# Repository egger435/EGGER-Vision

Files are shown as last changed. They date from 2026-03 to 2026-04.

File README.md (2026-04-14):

# EGGER Vision

基于Unity上位机 + STM32下位机 + 树莓派视觉模块的远程遥控车项目

## 一、ta是神马东西？

<p align="center">
    <a>
        
        <br>
    </a>
</p>

视频地址：https://www.bilibili.com/video/BV1trXPBxEZR

&emsp;&emsp;这是一个**完整远程控制小车项目**，包含：

* stm32控制板硬件连接电路
* 车身3d打印结构
* 嵌入式控制程序
* Unity可视化客户端

&emsp;&emsp;实现了：

* 手柄/键盘双模式远程控制
* 实时视频流传输

## 二、ta的组成是？

### 2.1 用了哪些东西

&emsp;&emsp;***硬件部分***：

  1. **stm32f103c8t6最小系统板**: 控制电机、舵机、处理底层控制逻辑
  2. **tb6612电机驱动模块**: 驱动电机
  3. **树莓派4b视觉模块（包括摄像头）**: 采集并发送视频流、接收控制信号
  4. **SG90舵机**: 转向前桥控制、摄像头转向
  5. **lm2596电源模块**: 供电
  6. **12V 18650可充电池组**：供电
  7. **拼夕夕的带有转向前桥的底盘**
  8. **3D打印结构**: 支架、连接件、挂车等

&emsp;&emsp;***软件部分***:

  1. **Unity2022.3.62f2c1**: 远程控制客户端开发
  2. **基于UDP的Unity和树莓派远程通信**: 这部分可以查看我的另一个仓库
     https://github.com/egger435/Unity-Pi-connect
  3. **在EIDE中使用库函数开发的stm32**

### 2.2 小车的架构

<p align="center">
    <a>
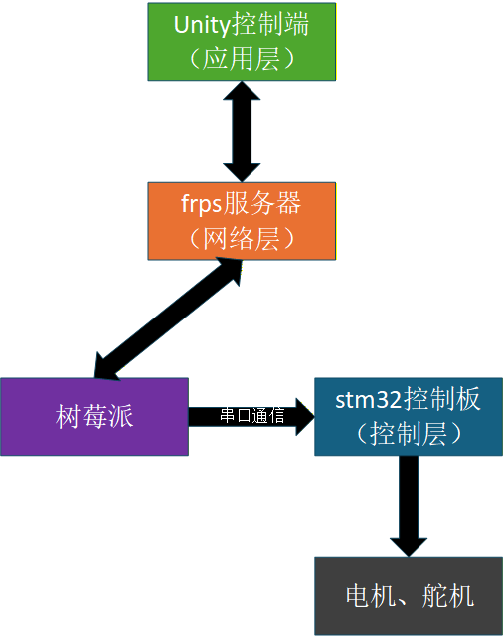
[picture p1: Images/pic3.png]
        
        <br>
    </a>
</p>

### 2.3 项目的架构

#### * Board文件夹

&emsp;&emsp;stm32控制板PCB设计文件, 线路就是简单的连连看。初中生来了都能看懂。

#### * Pi文件夹

&emsp;&emsp;树莓派视频流捕获和传输以及接收控制信号的代码

#### * SolidWorksFiles文件夹

&emsp;&emsp;***除了底盘外***的整车的3D结构模型, 包括3D打印件

#### * STM32文件夹

&emsp;&emsp;在EIDE中使用库函数开发的嵌入式控制代码

#### * UnityClient文件夹

&emsp;&emsp;Unity控制客户端工程文件

## 三、ta是怎么工作的

<p align="center">
    <a>
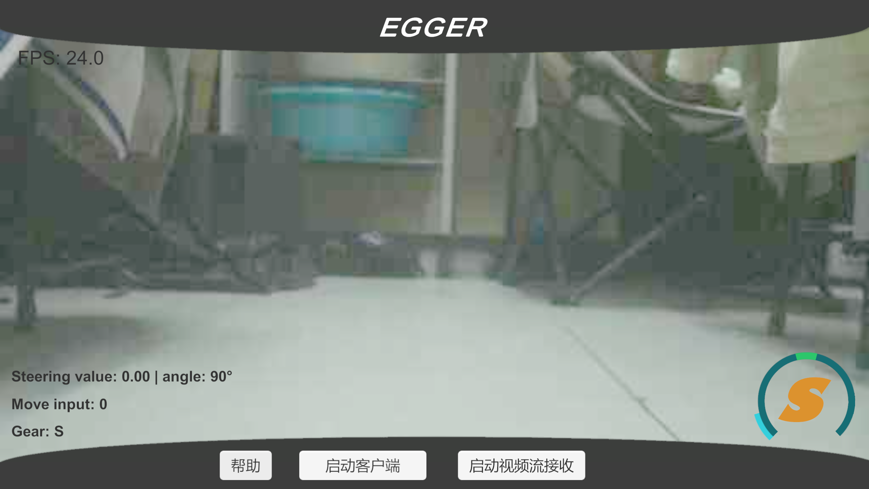
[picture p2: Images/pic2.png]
        
        <br>
    </a>
</p>

&emsp;&emsp;首先，Unity客户端会读取同目录下的`client_config`配置文件，得到服务器IP地址等信息。

&emsp;&emsp;然后，启动客户端的时候就会根据配置文件上的信息初始化。接着等待树莓派程序启动就可以接收视频流了。

&emsp;&emsp;简单来说就是，用户可以在Unity客户端实时看到画面，然后用手柄就能控制小车了。无论用户在哪，只要有网络就行。

&emsp;&emsp;信号流的传递：手柄 → Unity → FRPS服务器 → 树莓派 → stm32控制板

## ta的广告语

* 拖了个挂车，有**更大的储物空间**🚚
* 舵机控制转向加线性电门扳机，带来**更精准的操控**🦽
* 前置摄像头，拥有第一人称的**驾驶乐趣**🏎️
* 远程网络通信，能让你**在地球另一端控制它**🌍
* 还有后视镜，**足不出户**练习停车技巧
* 堪比奥迪夸戳的全史四驱系统:P

## 用户评价

某个不透露姓名的买家：

已购入，不建议入手[发怒]

速度太慢了，本来买来还想帮我跑校园跑的，结果比我走的还慢，别叫Vision叫蜗牛吧[发怒]

有转向前桥却没有阿克曼转向，也没有差速器，过弯表现一塌糊涂，转弯半径比我奶奶的破三轮都大[发怒]

延迟太不稳定了，一到信号不好的地方帧率就蹭蹭掉[发怒]

画质太差了，纯纯马赛克

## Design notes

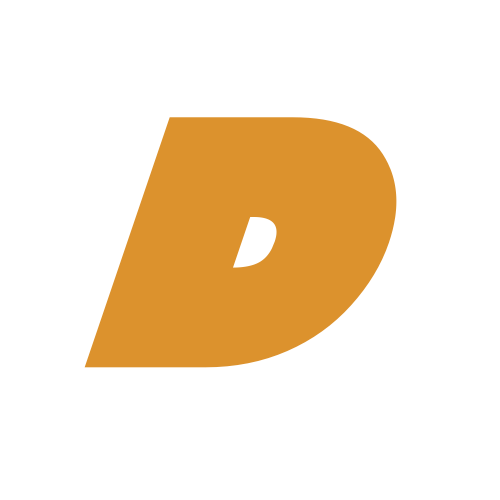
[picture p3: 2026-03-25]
UnityClient/Assets/Resource/D.png

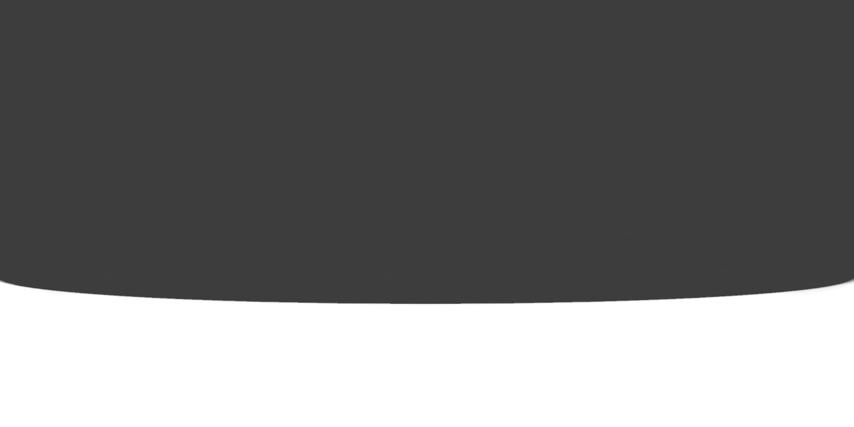
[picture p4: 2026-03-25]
UnityClient/Assets/Resource/upImage.png

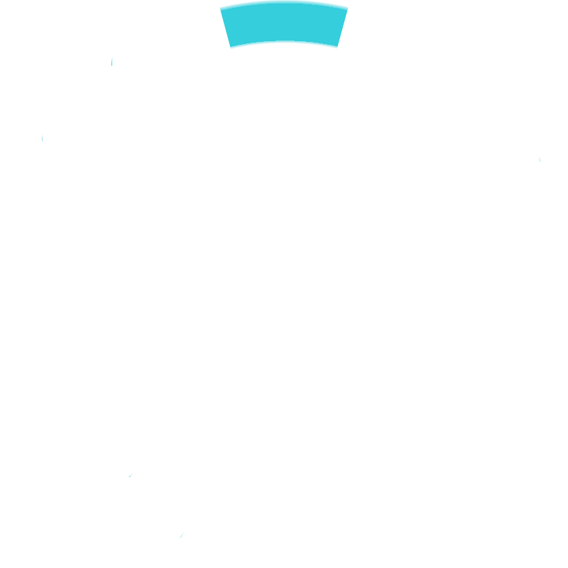
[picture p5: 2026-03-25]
UnityClient/Assets/Resource/steeringPos.png

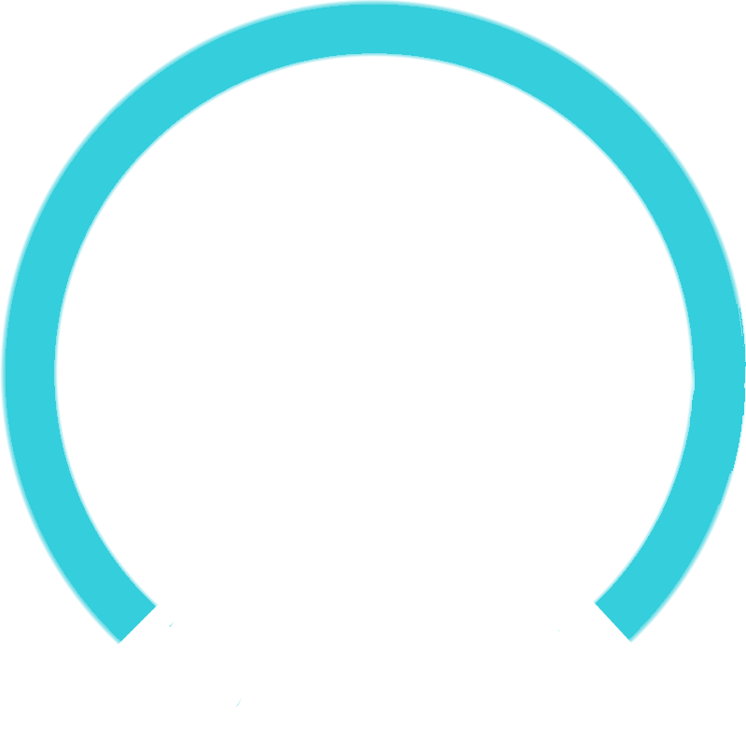
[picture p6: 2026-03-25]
UnityClient/Assets/Resource/Fill.png

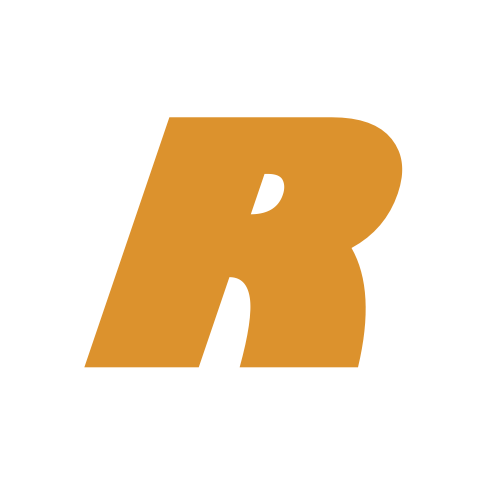
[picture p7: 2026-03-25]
UnityClient/Assets/Resource/R.png

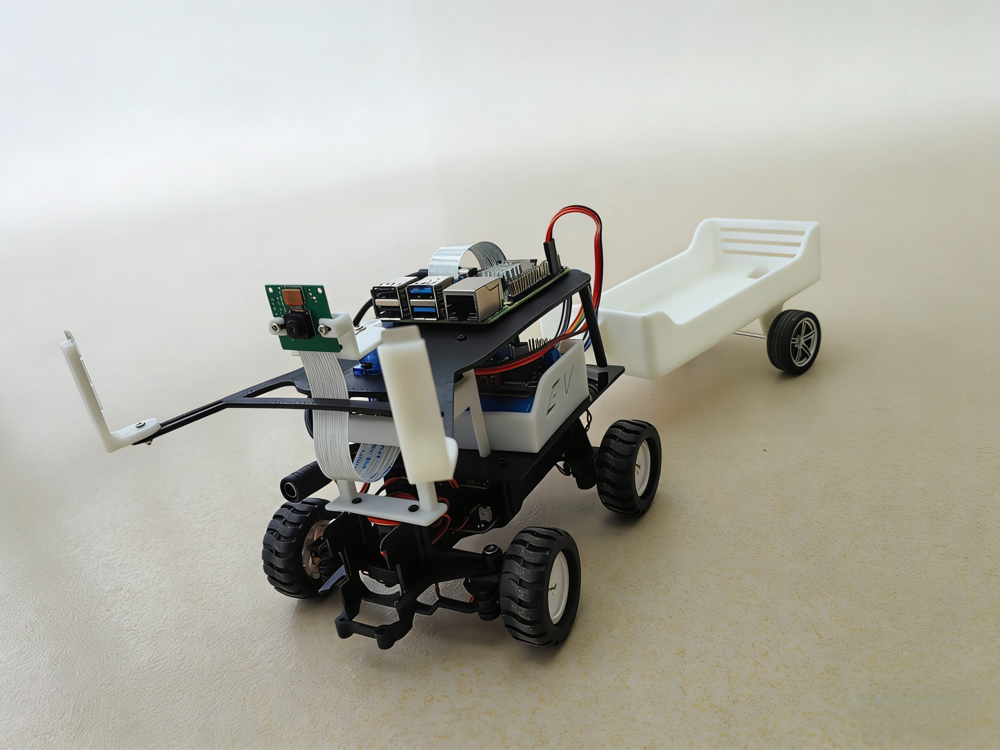
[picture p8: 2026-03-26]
UnityClient/Assets/Resource/bkg.png

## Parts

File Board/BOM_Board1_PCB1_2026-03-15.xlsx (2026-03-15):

No. | Quantity | Comment | Designator | Footprint | Value | Manufacturer Part | Manufacturer | Supplier Part | Supplier
1 | 3 | 2.54-1*3P针 | H1,H2,H3 | HDR-TH_3P-P2.54-V-M-1 |  | 2.54-1*3P针 | BOOMELE(博穆精密) | C49257 | LCSC
2 | 1 | PZ2.54-2*5 | H4 | HDR-TH_10P-P2.54-V-M-R2-C5-S2.54-1 |  | PZ2.54-2*5 | ZHOURI(洲日) | C5156677 | LCSC
3 | 1 | 1kΩ | R1 | R0603 | 1kΩ | 0603WAF1001T5E | UNI-ROYAL(厚声) | C21190 | LCSC
4 | 4 | KH-2.54FH-1X20P-H8.5 | U1,U2,U8,U9 | HDR-TH_20P-P2.54-V-F-2 |  | KH-2.54FH-1X20P-H8.5 | kinghelm(金航标) | C2905423 | LCSC
5 | 1 | PZ2.54-2*4 | U7 | HDR-TH_8P-P2.54-V-M-R2-C4-S2.54 |  | PZ2.54-2*4 | ZHOURI(洲日) | C5156676 | LCSC
6 | 4 | ZX-MX1.25-2PZZ | U10,U11,U12,U13 | CONN-TH_2P-P1.25_MEGASTAR_ZX-MX1.25-2PZZ |  | ZX-MX1.25-2PZZ | Megastar(兆星) | C7430458 | LCSC
7 | 1 | KT-0603R | 状态LED | LED_0603 |  | KT-0603R | KENTO | C2286 | LCSC

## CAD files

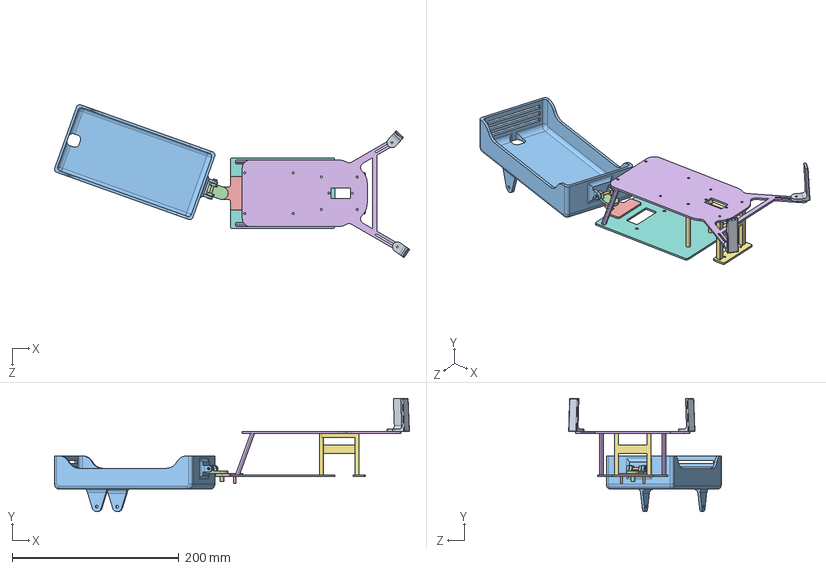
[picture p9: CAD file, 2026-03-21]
SolidWorksFiles/装配.SLDASM
425.7 x 135.9 x 183.2 mm
底板(非舵机转向板)
二层支架_2
二层板
挂车连接件
挂车连接件2
挂车
挂车连接件3
后视镜 x 2

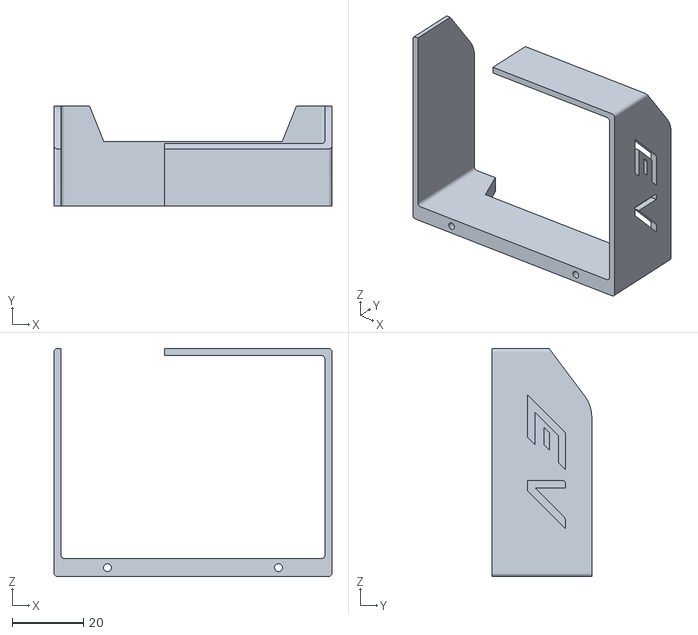
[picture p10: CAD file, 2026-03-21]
SolidWorksFiles/3dprint/电源固定件_3dprint.STL
78.0 x 28.0 x 64.0

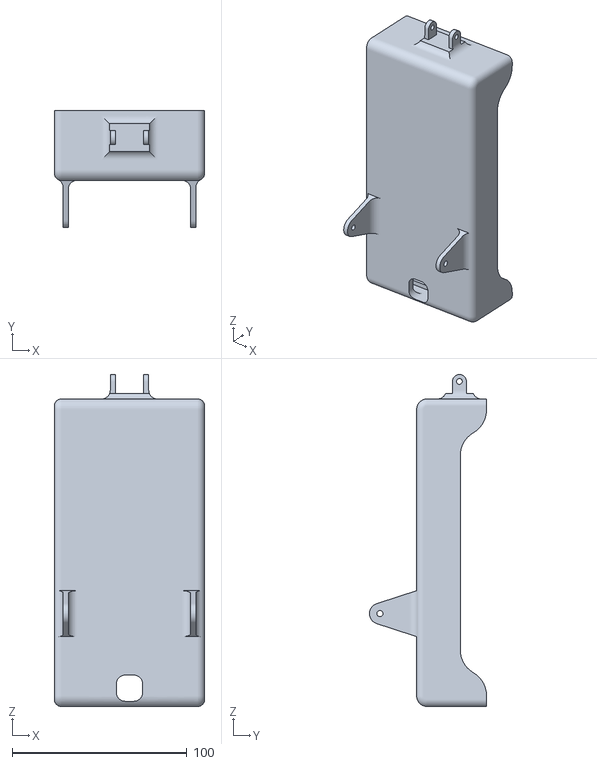
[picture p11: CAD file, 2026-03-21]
SolidWorksFiles/3dprint/挂车_3dprint.STL
86.0 x 67.0 x 190.0

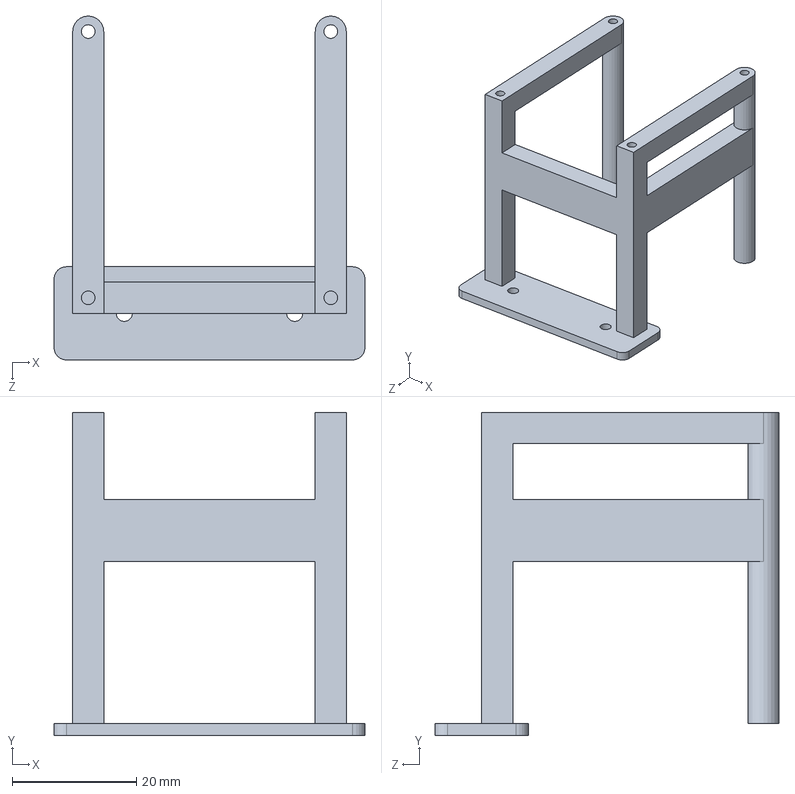
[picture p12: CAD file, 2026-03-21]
SolidWorksFiles/二层支架_2.SLDPRT
50.0 x 52.0 x 55.3 mm

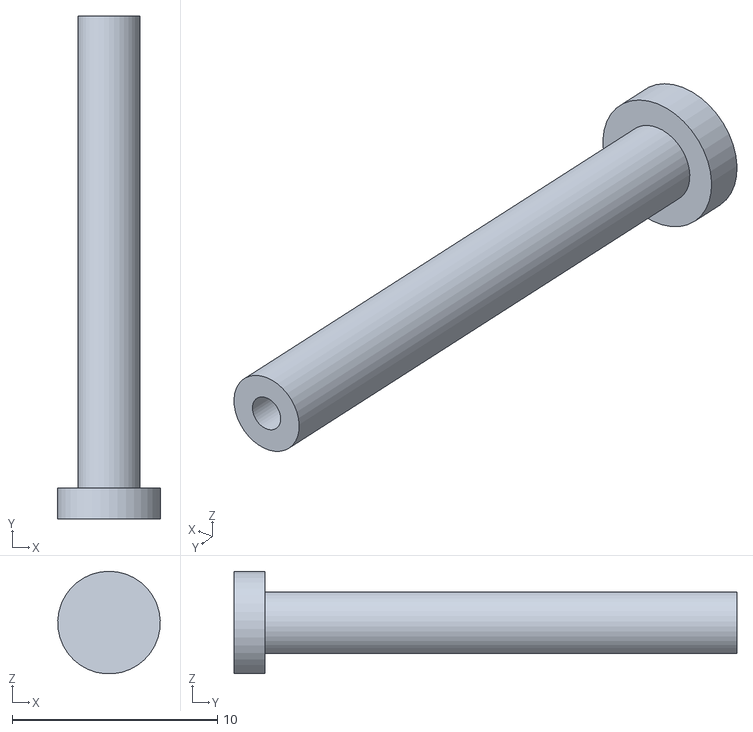
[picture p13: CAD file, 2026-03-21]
SolidWorksFiles/3dprint/挂车连接件3_3dprint.STL
5.00 x 24.5 x 4.99

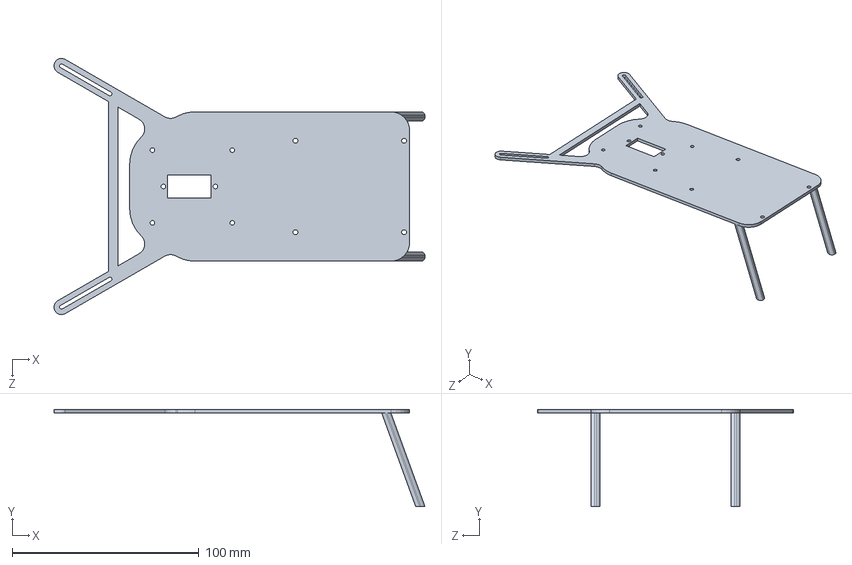
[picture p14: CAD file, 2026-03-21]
SolidWorksFiles/二层板.SLDPRT
198.7 x 52.0 x 137.3 mm

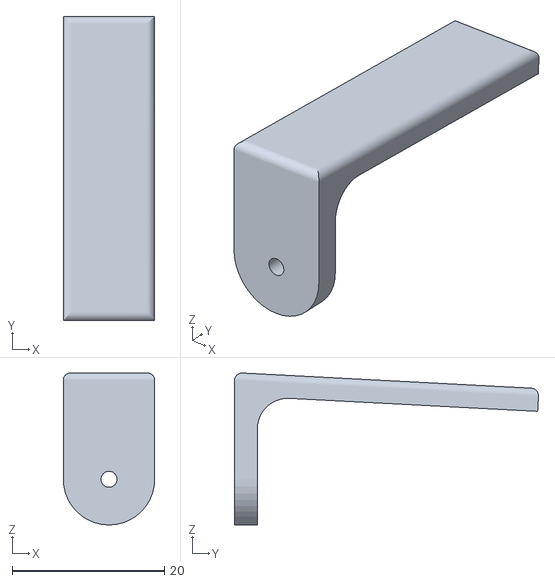
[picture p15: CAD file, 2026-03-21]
SolidWorksFiles/3dprint/后视镜_3dprint.STL
12.0 x 39.9 x 19.9

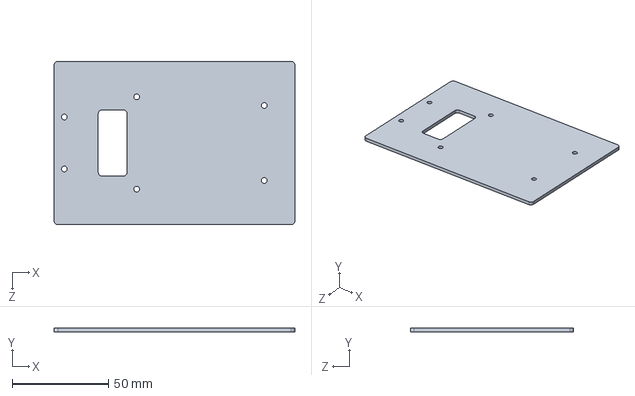
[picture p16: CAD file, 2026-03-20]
SolidWorksFiles/底板(非舵机转向板).SLDPRT
125.3 x 2.00 x 85.0 mm

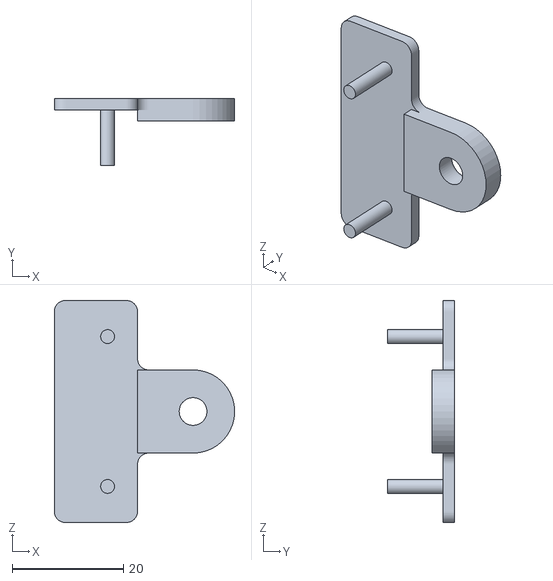
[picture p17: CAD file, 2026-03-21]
SolidWorksFiles/3dprint/挂车连接件_3dprint.STL
32.5 x 12.0 x 40.0

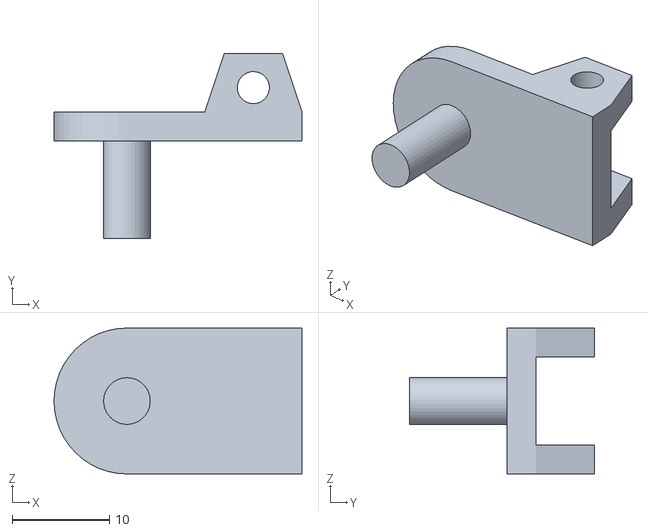
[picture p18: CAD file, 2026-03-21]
SolidWorksFiles/3dprint/挂车连接件2_3dprint.STL
25.5 x 19.0 x 15.0

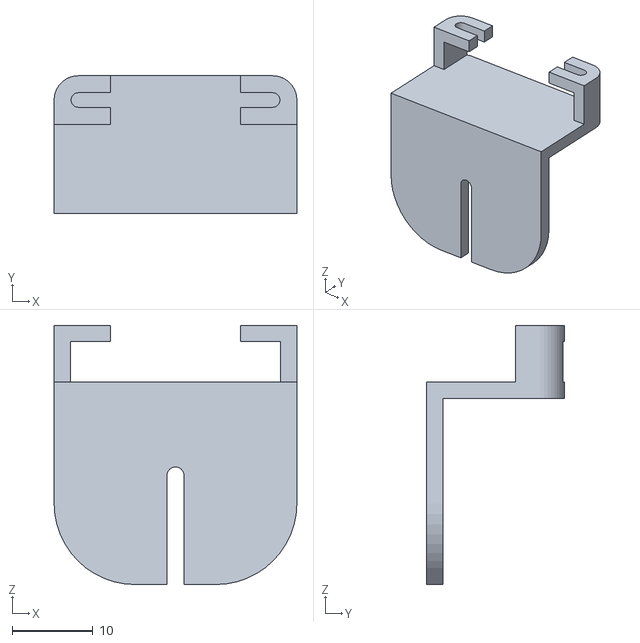
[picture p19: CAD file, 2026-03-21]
SolidWorksFiles/3dprint/摄像头固定件_3dprint.STL
30.0 x 17.0 x 32.0

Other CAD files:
SolidWorksFiles/后视镜.SLDPRT
SolidWorksFiles/3dprint/二层板_3dprint.STL
SolidWorksFiles/挂车.SLDPRT
SolidWorksFiles/3dprint/二层支架_2_3dprint.STL
SolidWorksFiles/挂车连接件3.SLDPRT
SolidWorksFiles/挂车连接件.SLDPRT
SolidWorksFiles/挂车连接件2.SLDPRT
SolidWorksFiles/摄像头固定件.SLDPRT
SolidWorksFiles/电源固定件.SLDPRT

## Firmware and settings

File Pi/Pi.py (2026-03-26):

import serial
import socket
import struct
import threading
import time
import cv2
from picamera2 import Picamera2 # pyright: ignore[reportMissingImports]

# UDP 指令接收端配置
UDP_CTRL_IP    = "0.0.0.0"
UDP_CTRL_PORT  = 12345          # 树莓派端监听frp服务器端口, 和树莓派frpc.toml中的localPort一致

# UDP 视频流发送端配置
SEND_VIDEO     = True
SERVER_IP      = "服务器公网ip地址"
UDP_VIDEO_PORT = 13300          # 树莓派端向frp服务器发送消息的端口, 和Unity端frpc.toml中的remotePort一致
RESOLUTION     = (512, 256)    # 视频分辨率
FPS            = 30             # 视频帧率
CHUNK_SIZE     = 1024           # 视频帧分片大小
JPEG_QUALITY   = 50             # JPEG压缩质量

global log_index
log_index = 0

ser = serial.Serial("/dev/ttyS0", baudrate=115200, timeout=0.01)  # 建立串口通信
print(f"[SERIAL] Serial start; l_i: {log_index}")
log_index += 1

# 建立socket客户端
sock = socket.socket(socket.AF_INET, socket.SOCK_DGRAM)
sock.bind((UDP_CTRL_IP, UDP_CTRL_PORT))
print(f"[CTRL] UDP listening on {UDP_CTRL_PORT}; l_i: {log_index}")
log_index += 1

# 视频流传输线程    
def video_stream_thread():
    global log_index
    # 摄像头初始化
    picam = Picamera2()
    config = picam.create_video_configuration(
        main={"size":RESOLUTION, "format":"RGB888"}
    )
    picam.configure(config)
    picam.set_controls({"FrameRate":FPS})
    picam.start()
    time.sleep(1)
    encode_param = [int(cv2.IMWRITE_JPEG_QUALITY), JPEG_QUALITY]
    
    sock = socket.socket(socket.AF_INET, socket.SOCK_DGRAM)
    print(f"[VIDEO] Start sending to {SERVER_IP}:{UDP_VIDEO_PORT}; l_i: {log_index}")
    log_index += 1
    frame_id = 0
    
    while True:
        array = picam.capture_array()

        _, jpeg_data = cv2.imencode('.jpg', array, encode_param)
        frame_data = jpeg_data.tobytes()
        
        # 帧数据分片
        chunks = [frame_data[i:i+CHUNK_SIZE] for i in range(0, len(frame_data), CHUNK_SIZE)]
        total_chunks = len(chunks)
        
        # 发送帧标识和帧分片
        for idx, chunk in enumerate(chunks):
            header = struct.pack('>IHH',  # 大端
                                 frame_id, 
                                 total_chunks, 
                                 idx
                                 )  
            sock.sendto(header + chunk, (SERVER_IP, UDP_VIDEO_PORT))
        
        frame_id += 1

# 接收控制数据
def recv_cmd():
    global log_index
    data, addr = sock.recvfrom(32)
    cmd = data.decode("utf-8").strip()
    print(f"[CTRL] Received cmd: '{cmd}' from {addr}; l_i: {log_index}")
    log_index += 1

    ser_cmd = '@' + cmd + '*'  # 加上串口指令首部尾部
    ser.write(ser_cmd.encode("utf-8"))
    ser.flush()
    print(f"[SERIAL] Sent to STM32: {ser_cmd}; l_i: {log_index}")
    log_index += 1

def main():
    if SEND_VIDEO:
        # 视频流发送子线程
        t_video = threading.Thread(target=video_stream_thread, daemon=True)
        t_video.start()

    # 主线程接收控制数据
    while True:
        recv_cmd()

if __name__ == "__main__":
    main()
    

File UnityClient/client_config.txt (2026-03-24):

SeverIP = frpsIP地址
MsgSendPort = 12300
MsgReceivePort = 13300
FrpSetupBat = frpc_setup.bat

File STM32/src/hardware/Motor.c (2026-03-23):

#include "Motor.h"

uint8_t Motor_State;  // 电机状态 1前进 0后退 2停止

// 电机初始化
void Motor_Init(void)
{
    Motor_PWM_Init();
    Motor_PWM_SetCompare2(0);

    // GPIO初始化
    RCC_APB2PeriphClockCmd(RCC_APB2Periph_AFIO, ENABLE);
    GPIO_PinRemapConfig(GPIO_Remap_SWJ_JTAGDisable, ENABLE);  // 释放PB3 PB4
    RCC_APB2PeriphClockCmd(RCC_APB2Periph_GPIOB, ENABLE);

    GPIO_InitTypeDef GPIO_InitStructure;
    GPIO_InitStructure.GPIO_Mode = GPIO_Mode_Out_PP;
    GPIO_InitStructure.GPIO_Pin = FRONT_LEFT_PIN_1 | FRONT_LEFT_PIN_2 | FRONT_RIGHT_PIN_1 | FRONT_RIGHT_PIN_2 |
                                  REAR_LEFT_PIN_1  | REAR_LEFT_PIN_2  | REAR_RIGHT_PIN_1  | REAR_RIGHT_PIN_2;
    GPIO_InitStructure.GPIO_Speed = GPIO_Speed_50MHz;
    GPIO_Init(MOTOR_GPIO, &GPIO_InitStructure);

    Motor_Set_Speed(0);

    Motor_Stop();
}

// 设置电机转速
void Motor_Set_Speed(uint8_t speed)
{
    if (speed > 100) speed = 100;
    Motor_PWM_SetCompare2(speed);
}

void Motor_Reverse(void)
{
    GPIO_SetBits(MOTOR_GPIO, FRONT_LEFT_PIN_1);
    GPIO_ResetBits(MOTOR_GPIO, FRONT_LEFT_PIN_2);

    GPIO_SetBits(MOTOR_GPIO, FRONT_RIGHT_PIN_1);
    GPIO_ResetBits(MOTOR_GPIO, FRONT_RIGHT_PIN_2);

    GPIO_SetBits(MOTOR_GPIO, REAR_LEFT_PIN_1);
    GPIO_ResetBits(MOTOR_GPIO, REAR_LEFT_PIN_2);

    GPIO_SetBits(MOTOR_GPIO, REAR_RIGHT_PIN_1);
    GPIO_ResetBits(MOTOR_GPIO, REAR_RIGHT_PIN_2);
    
    Motor_State = 0;
}

void Motor_Forward(void)
{
    GPIO_ResetBits(MOTOR_GPIO, FRONT_LEFT_PIN_1);
    GPIO_SetBits(MOTOR_GPIO, FRONT_LEFT_PIN_2);

    GPIO_ResetBits(MOTOR_GPIO, FRONT_RIGHT_PIN_1);
    GPIO_SetBits(MOTOR_GPIO, FRONT_RIGHT_PIN_2);

    GPIO_ResetBits(MOTOR_GPIO, REAR_LEFT_PIN_1);
    GPIO_SetBits(MOTOR_GPIO, REAR_LEFT_PIN_2);

    GPIO_ResetBits(MOTOR_GPIO, REAR_RIGHT_PIN_1);
    GPIO_SetBits(MOTOR_GPIO, REAR_RIGHT_PIN_2);

    Motor_State = 1;
}

void Motor_Stop(void)
{
    GPIO_SetBits(MOTOR_GPIO, FRONT_LEFT_PIN_1);
    GPIO_SetBits(MOTOR_GPIO, FRONT_LEFT_PIN_2);

    GPIO_SetBits(MOTOR_GPIO, FRONT_RIGHT_PIN_1);
    GPIO_SetBits(MOTOR_GPIO, FRONT_RIGHT_PIN_2);

    GPIO_SetBits(MOTOR_GPIO, REAR_LEFT_PIN_1);
    GPIO_SetBits(MOTOR_GPIO, REAR_LEFT_PIN_2);

    GPIO_SetBits(MOTOR_GPIO, REAR_RIGHT_PIN_1);
    GPIO_SetBits(MOTOR_GPIO, REAR_RIGHT_PIN_2);

    Motor_State = 2;
}

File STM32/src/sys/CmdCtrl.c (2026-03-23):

#include "CmdCtrl.h"
#include "string.h"
#include "stdlib.h"

CarGear cur_gear = GEAR_NEUTRAL;  // 默认空档

uint8_t speed_coefficient = 0;    // 速度系数, 用于控制挡位

void Cmd_Change_LED_State(char *args);        // LCS, 改变LED灯状态

void Cmd_Rotate_Camera_Left(char *args);      // RCL, 左转摄像头
void Cmd_Rotate_Camera_Right(char *args);     // RCR, 右转摄像头
void Cmd_Rotate_Camera_Behind(char *args);    // RCB, 倒转摄像头
void Cmd_Rotate_Camera_in_Place(char *args);  // RCP, 摄像头归位

void Cmd_Steering_Servo_Angle(char *args);    // SSA, 设置方向舵机角度

void Cmd_Shift_Gear(char *args);              // SG, 切换挡位
void Cmd_Motor_Speed(char *args);             // MS, 设置电机速度

// 指令表
static const CmdEntry cmd_Table[] = 
{
    {"MS", Cmd_Motor_Speed},
    {"SSA", Cmd_Steering_Servo_Angle},
    {"SG", Cmd_Shift_Gear},
    {"RCL", Cmd_Rotate_Camera_Left},
    {"RCR", Cmd_Rotate_Camera_Right},
    {"RCB", Cmd_Rotate_Camera_Behind},
    {"RCP", Cmd_Rotate_Camera_in_Place},
    {"LCS", Cmd_Change_LED_State},
    {NULL, NULL}  // 表尾标记
};

// 提取指令, 输出指令的参数部分, out_cmd中为指令部分
static char* Cmd_ExtractCommand(char *cmd, char *out_cmd)
{
    char *colon = strchr(cmd, ':');
    int cmd_len = colon ? (colon - cmd) : strlen(cmd);

    strncpy(out_cmd, cmd, cmd_len);
    out_cmd[cmd_len] = '\0';
    return colon ? (colon + 1) : "";
}

// 根据cmd执行指令
void Cmd_Ctrl(char *cmd)
{
    if (cmd == NULL || strlen(cmd) == 0) return;

    // 提取指令参数信息
    char cmd_name[10];
    char *args = Cmd_ExtractCommand(cmd, cmd_name);

    // 查找指令表
    for (int i = 0; cmd_Table[i].cmd_name != NULL; i++)
    {
        if (strcmp(cmd_name, cmd_Table[i].cmd_name) == 0)
        {
            cmd_Table[i].handler(args);
            return;
        }
    }
}

// 改变LED状态
void Cmd_Change_LED_State(char *args)
{
    TestLED_Toggle();
}

// 控制摄像头左转
void Cmd_Rotate_Camera_Left(char *args)
{
    Cam_Servo_RotateLeft();
}

// 控制摄像头右转
void Cmd_Rotate_Camera_Right(char *args)
{
    Cam_Servo_RotateRight();
}

// 控制摄像头向后转
void Cmd_Rotate_Camera_Behind(char *args)
{
    // TODO: 控制摄像头舵机向后转
}

// 控制摄像头归位
void Cmd_Rotate_Camera_in_Place(char *args)
{
    Cam_Servo_ResetPos();
}

// 设置方向舵机角度
void Cmd_Steering_Servo_Angle(char *args)
{
    // 获取目标角度值
    int targetAngle = atoi(args);
    Steering_Servo_SetAngle(targetAngle);
}

// 切换档位
void Cmd_Shift_Gear(char *args)
{
    char gear = args[0];
    switch(gear)
    {
        case 'N': cur_gear = GEAR_NEUTRAL; speed_coefficient = 0; Motor_Stop();    break;
        case 'D': cur_gear = GEAR_DRIVE;   speed_coefficient = 1; Motor_Forward(); break;
        case 'S': cur_gear = GEAR_SPEED;   speed_coefficient = 2; Motor_Forward(); break;
        case 'R': 
            cur_gear = GEAR_REVERSE;
            reverse_gear_LED_State = 0;
            LED_Timer = 0;
            speed_coefficient = 1;
            Motor_Reverse();
            break;
        default: cur_gear = GEAR_NEUTRAL; break;
    }
}

void Cmd_Motor_Speed(char *args)
{
    int targetSpeed = atoi(args) / 2;
    targetSpeed *= speed_coefficient;
    Motor_Set_Speed(targetSpeed);
}

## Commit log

2025-11-10 upload stm32
2025-11-10 配置STM32串口
    配置STM32工程环境，串口初始化
2025-11-11 LED小灯测试成功
    xbox手柄控制小灯
    树莓派串口与stm32通信
    时延问题有待解决
    [Pi.py]
2025-11-12 创建指令表
    函数指针控制指令执行
2026-01-17 Unity添加按键动作
    摄像头转向、获取扳机输入
2026-01-28 Update Pi.py
    修改注释，更新ip地址
2026-01-28 添加舵机控制
2026-01-28 更新目录结构
2026-01-30 Update Serial.c
    修改蓝牙模式下的波特率为9600
2026-01-31 添加方向舵机功能
2026-03-05 修改视频流传输协议
2026-03-09 完成舵机控制
    完成方向舵机连续控制，摄像头舵机控制
2026-03-10 完成档位灯光状态显示
2026-03-12 转向舵机安装完成
2026-03-13 绘制stm32控制板原理图
2026-03-14 控制板pcb板绘制完成
2026-03-15 生成BOM和坐标文件
    [BOM_Board1_PCB1_2026-03-15.xlsx, PickAndPlace_PCB1_2026_03_15.xlsx]
2026-03-16 优化视频流传输编码，加入转向舵机偏置
2026-03-17 结构件建模
    [二层支架_2.SLDPRT, 底板(非舵机转向板).SLDPRT, 电源固定件.SLDPRT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]
2026-03-18 设计摄像头固定件和二层板
    [二层板.SLDPRT, 摄像头固定件.SLDPRT, 装配.SLDASM]
2026-03-19 修改二层板
    [二层支架_2.SLDPRT, 二层板.SLDPRT, 电源固定件.SLDPRT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]
2026-03-20 挂车及其连接件设计完成
    [底板(非舵机转向板).SLDPRT, 挂车.SLDPRT, 挂车连接件.SLDPRT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]
2026-03-21 完成3d打印件设计并修改视频分辨率
    [二层板.SLDPRT, 后视镜.SLDPRT, 装配.SLDASM]
2026-03-21 生成3d打印文件
    [二层支架_2.SLDPRT, 二层支架_2_3dprint.STL, 二层板_3dprint.STL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]
2026-03-23 完成电机控制功能
2026-03-24 修改Unity客户端UI布局
    [client_config.txt]
2026-03-25 修改UI
2026-03-26 小车组装完成
2026-03-26 更改UI
2026-03-26 添加README
